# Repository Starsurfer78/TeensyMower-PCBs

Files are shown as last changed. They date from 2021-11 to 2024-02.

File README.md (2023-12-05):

DIY Robot Lawn Mower Community: https://www.diy-robot-lawn-mower.com/

# Teensymower PCB's - DIY Robot Lawn Mower (Teensy 4.1) 

The PCB's are designed to get you started on your own robotic lawnmower project. 
It doesn't matter if you want to convert a commercial mower or use a 3D printed housing.

The TeensyMainPCB is the brain of the mower to which all sensors and motors are connected.
The PowerPCB is responsible for the power supply and monitoring of the battery and the motors. 
The Wifi SenderPCB is responsible for the perimeter cable and goes into the charging station of the mower.

For your DIY project you need all 3 Boards.

RTK GPS is not yet possible at the moment

Only a few Electronic Parts are needed. 
- JST-XH Connectors
- Screw Terminal 5.04mm
- Resistors
- Pin Header Connector 2.54mm
- Active Buzzer
- LED
- Jumper
- Teensy 4.1
- ESP32 DEV Kit V1

Attention: 
The PCB's are still under development.
If you want to order your own PCBs, please check the forum first to see if there are any problems.
Use the PCBs at your own risk, no liability is assumed.

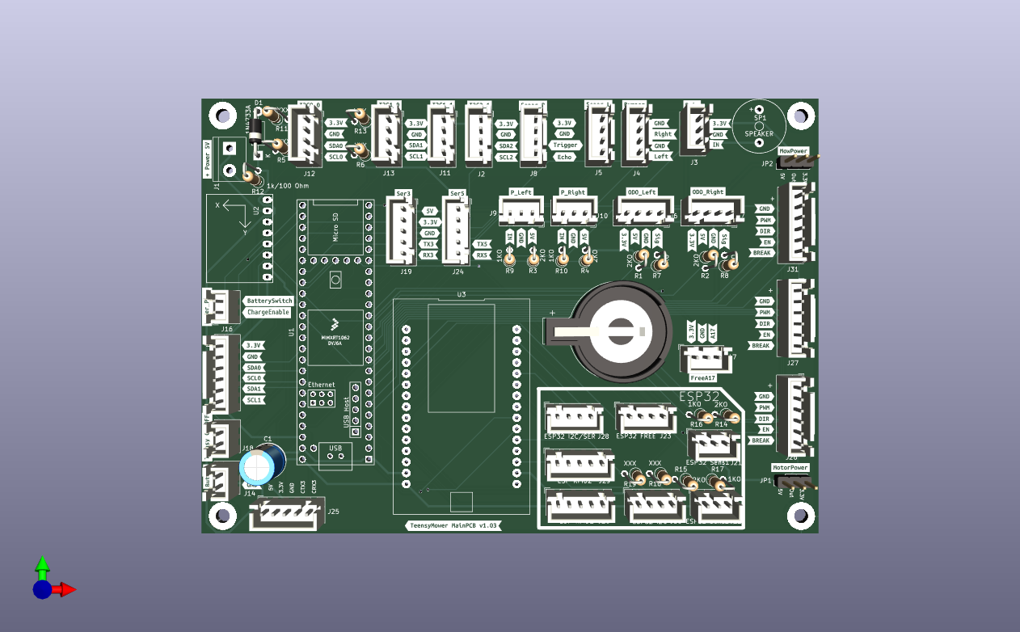
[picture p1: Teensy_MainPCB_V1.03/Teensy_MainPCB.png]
Vorschau Teensy PCB


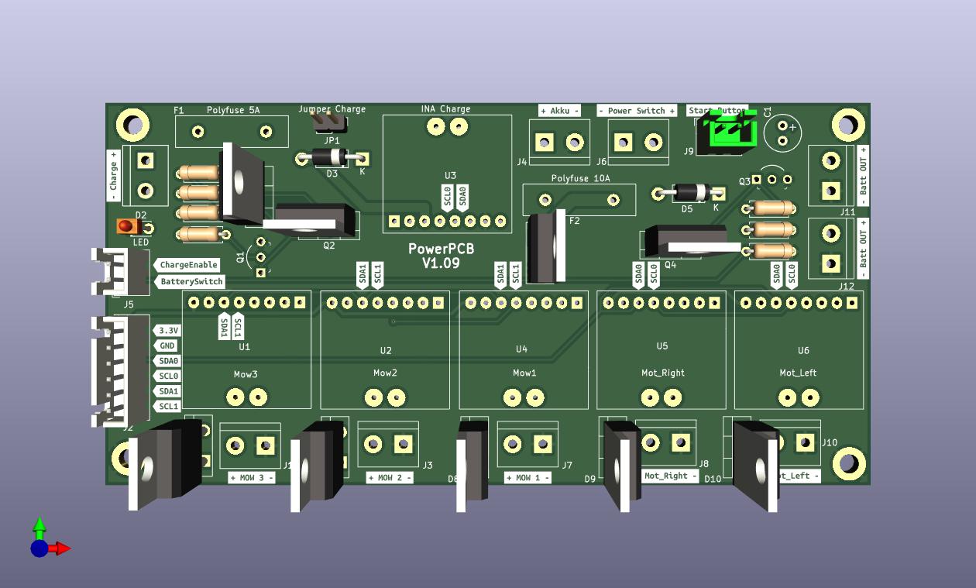
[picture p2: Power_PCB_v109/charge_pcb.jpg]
Vorschau Power PCB
)

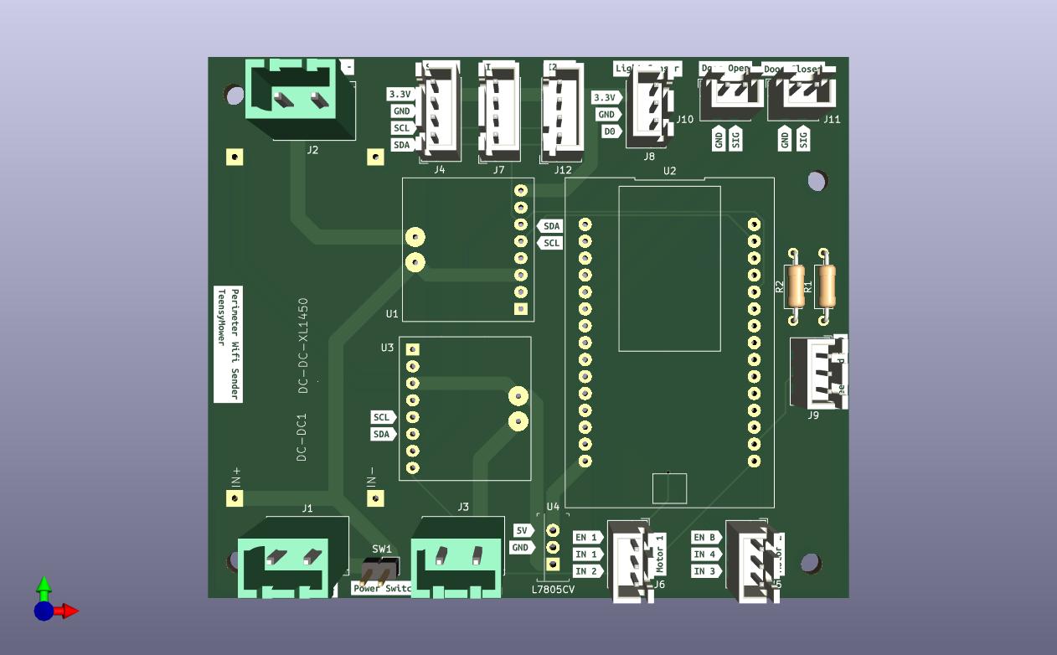
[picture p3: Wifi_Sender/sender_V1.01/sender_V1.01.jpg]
Vorschau WIFI Senderf PCB


Robomow RL2000:
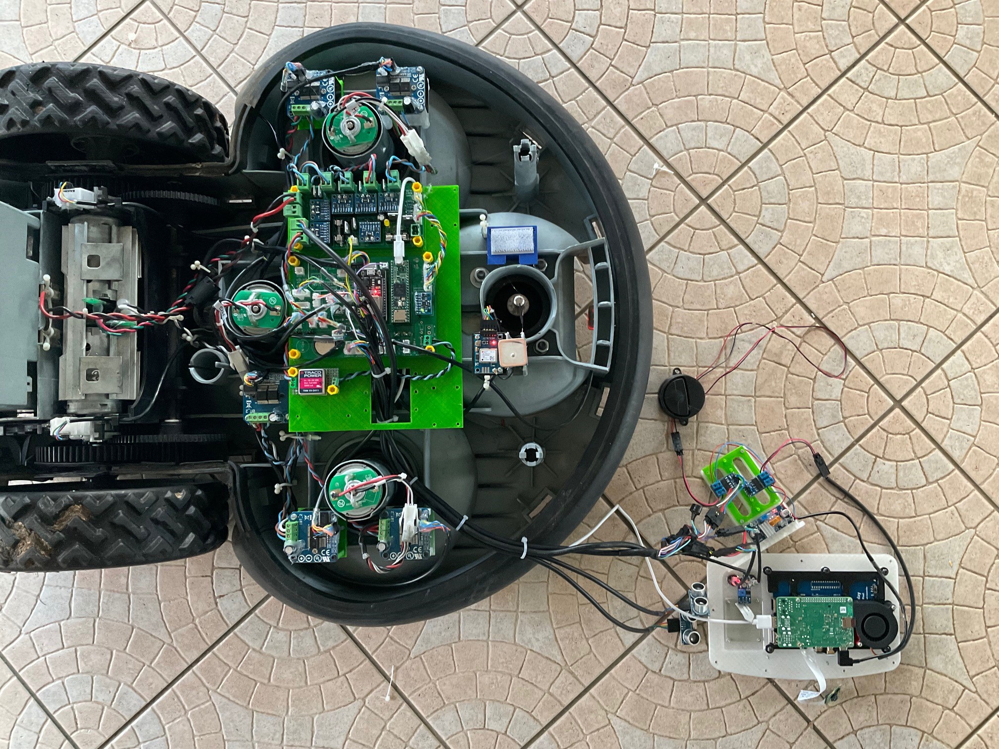
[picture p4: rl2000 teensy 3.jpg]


Tianchen TC-G158:
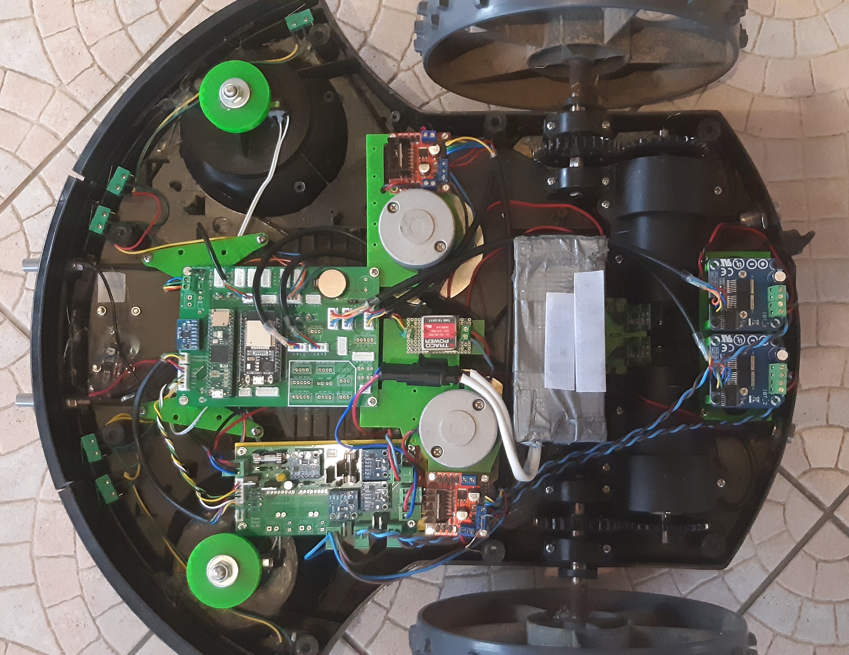
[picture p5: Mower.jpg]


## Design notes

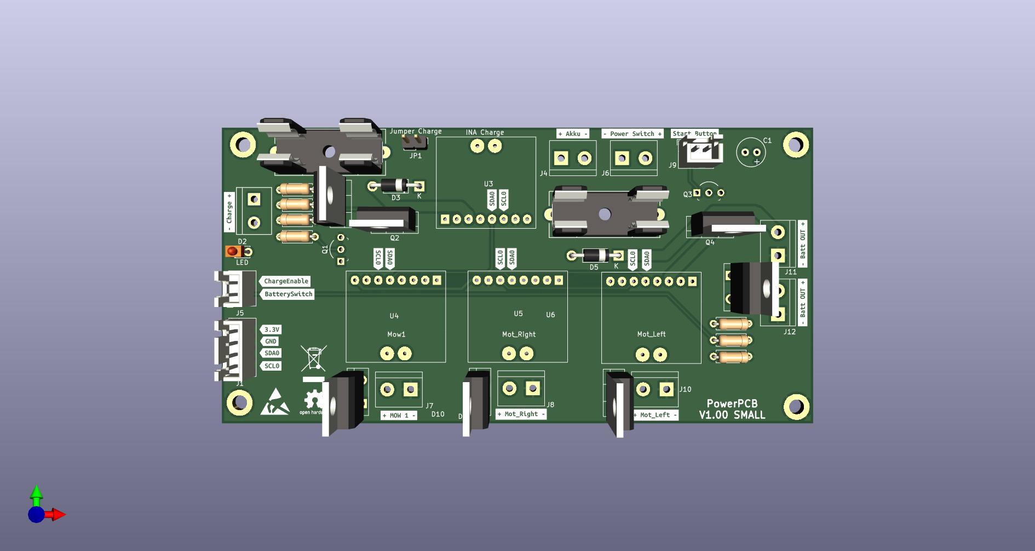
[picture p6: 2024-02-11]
Power_PCB_v100small/charge_pcb.jpg

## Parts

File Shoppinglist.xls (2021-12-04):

Quantidy | Name | Supplier
 | Präz.-Buchsenleisten 2,54 mm, 1X36, gerade | Reichelt (https://www.reichelt.de/praez-buchsenleisten-2-54-mm-1x36-gerade-mpe-115-1-036-p119957.html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)
 | 36pol. Stiftleiste, gerade, RM 2,54 | Reichelt (https://www.reichelt.de/36pol-stiftleiste-gerade-rm-2-54-sl-1x36g-2-54-p19504.html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)
 | Jumper 2,54 mm, geschlossen mit Griff | Reichelt (https://www.reichelt.de/jumper-2-54-mm-geschlossen-mit-griff-schwarz-mpe-149-4-002-f0-p119938.html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)
 | JST XH 2.54mm SET | Ebay (https://www.ebay.de/itm/203682351548?aid=1110006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)
 | JST XH 2.54mm 1x6 (PowerPCB) | Ebay (https://www.ebay.de/itm/194196796394?hash=item2d3707f3ea:g:1uUAAOSw9zZgwmGd)
 | Connection terminal system, 2-pin, spacing 5.08 | Reichelt (https://www.reichelt.de/de/en/connection-terminal-system-2-pin-spacing-5-08-akl-249-02-p36686.html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)
 | Box connector for AKL 249, 2-pin, spacing 5.08 | Reichelt (https://www.reichelt.de/de/en/box-connector-for-akl-249-2-pin-spacing-5-08-akl-220-02-p36693.html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)
 | LED Diode & Widerstände Sortiment Kit | Amazon (https://www.amazon.de/WayinTop-Widerstände-Sortiment-Arduino-Leuchtdiode/dp/B07YWX42RJ?pd)
 | Widerstand 1.5 Kohm | Amazon (https://www.amazon.de/gp/product/B07KX5B5DJ/ref=ppx_yo_dt_b_asin_title_o02_s00?ie=UTF8&psc=1)
 | Knopfzellenhalter Ø 20 mm | Reichelt (https://www.reichelt.de/knopfzellenhalter-fuer-20-mm-kzh-20-1-p44621.html?&trstct=pol_9&nbc=1)
 | INA226 | Amazon (https://www.amazon.de/gp/product/B07XM47JBW/ref=ppx_yo_dt_b_asin_title_o07_s01?ie=UTF8&psc=1)
 | INA3221 (Perimeter Sender) | Amazon (https://www.amazon.de/gp/product/B07XXFPNHC/ref=ppx_yo_dt_b_asin_title_o03_s01?ie=UTF8&psc=1)
 | 1N5819 Diode Schottky | Amazon (https://www.amazon.de/gp/product/B07KC2493L/ref=ppx_yo_dt_b_asin_title_o00_s00?ie=UTF8&psc=1)
 | IRF9540N 23 A 100 V | Amazon (https://www.amazon.de/gp/product/B086YW4TPD/ref=ppx_yo_dt_b_asin_title_o02_s00?ie=UTF8&psc=1)
 | MBR 1045 Schottkydiode, 45 V, 10 A | Reichelt (https://www.reichelt.de/schottkydiode-45-v-10-a-to-220ac-mbr-1045-p41944.html?search=MBR1045)
 | IRLB 8721 MOSFET, N-CH, TO-220, 30 V, 50 A, 65 W | Reichelt (https://www.reichelt.de/mosfet-n-ch-to-220-30-v-50-a-65-w-irlb-8721-p200919.html?search=IRLB+8721)
 | BC 547C Bipolartransistor, NPN, 45V, 0,1A, 0,5W | Reichelt (https://www.reichelt.de/bipolartransistor-npn-45v-0-1a-0-5w-to-92-bc-547c-p5007.html?search=BC547C)
 | Elko 100 uF, 100 V, 105°C | Reichelt (https://www.reichelt.de/de/en/e-cap-radial-100-uf-100-v-105-c-nhg-a-100u-100-p200367.html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)
 | Fuse holder, 5 x 20 mm, max. 6,3A/250V | Amazon (https://www.amazon.de/gp/product/B016UQPVLK/ref=ppx_yo_dt_b_asin_title_o01_s00?ie=UTF8&psc=1)
 | Glassicherung, 5 x 20 mm (10 A) | Amazon (https://www.amazon.de/SMIN-Stück-F10AL-Schnell-Blow-Sicherung/dp/B07Q98NDQQ?__mk_de_DE=ÅMÅŽÕÑ&s=diy)
 | Glassicherung, 5 x 20 mm (5 A) | Amazon (https://www.amazon.de/Stück-G-Sicherungseinsatz-Feinsicherung-5x20mm-522-524/dp/B01MV345Y5?__mk_de_DE=ÅMÅŽÕÑ&s=diy)
 | Buzzer 12mm 9,5mm RM 7,06 | Reichelt (https://www.reichelt.de/elektromagnetischer-summer-summer-tdb-05-p35918.html?&trstct=pol_0&nbc=1)
 | Push Button | Amazon (https://www.amazon.de/Larcele-Plastik-Momentary-Drücken-Druckknöpfe/dp/B077F7FT95)
 | Ein-Aus-Kippschalter | Amazon (https://www.amazon.de/Schalter-OFF-DPST-Terminals-wasserfester-Abdeckung/dp/B07438Q5ZZ?p)
 | Microswitch Bumper | Amazon (https://www.amazon.de/Hemobllo-Wasserdichter-Momentanschlag-Mikroschalter-Scharnierhebel/dp/B07LG18PN9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ÅMÅŽÕÑ)
 | Ultraschall JSN-SR04T (optional) | Amazon (https://www.amazon.de/gp/product/B08GLX5MHF/ref=ppx_yo_dt_b_asin_title_o08_s00?ie=UTF8&psc=1)
 | HC-SR04 Ultraschall (optional) | Amazon (https://www.amazon.de/AZDelivery-HC-SR04-Ultraschall-Entfernungsmesser-Raspberry/dp/B072N473HD)
 | Pn5180 NFC RFID (optional) | Amazon (https://www.amazon.de/gp/product/B07V1KZFNX/ref=ppx_yo_dt_b_asin_title_o09_s00?ie=UTF8&psc=1)
 | XL4015 5A DC-DC | Amazon (https://www.amazon.de/gp/product/B081JP5YZP/ref=ppx_yo_dt_b_asin_title_o08_s00?ie=UTF8&psc=1)
 | ESP32 DEV Kit v1 | Amazon (https://www.amazon.de/gp/product/B093GTDY9H/ref=ppx_yo_dt_b_asin_title_o01_s00?ie=UTF8&psc=1)
 | Teensy 4.1

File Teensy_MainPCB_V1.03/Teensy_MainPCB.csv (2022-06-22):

ID | Bezeichner | Gehäuse | Stückzahl | Bezeichnung | Anbieter und Referenz
1 | J2 | JST_XH_B4B-XH-A_1x04_P2.50mm_Vertical | 1 | I2C2_0
2 | J4 | JST_XH_B4B-XH-A_1x04_P2.50mm_Vertical | 1 | Bumper
3 | J5 | JST_XH_B4B-XH-A_1x04_P2.50mm_Vertical | 1 | Sonar_L
4 | J9 | JST_XH_B3B-XH-A_1x03_P2.50mm_Vertical | 1 | P_Left
5 | J10 | JST_XH_B3B-XH-A_1x03_P2.50mm_Vertical | 1 | P_Right
6 | J12 | JST_XH_B4B-XH-A_1x04_P2.50mm_Vertical | 1 | I2C0_0
7 | J13 | JST_XH_B4B-XH-A_1x04_P2.50mm_Vertical | 1 | I2C1_0
8 | J15 | JST_XH_B6B-XH-A_1x06_P2.50mm_Vertical | 1 | Power_PCB1
9 | R7,R8,R9,R10,R16,R17 | R_Axial_DIN0207_L6.3mm_D2.5mm_P2.54mm_Vertical | 6 | 1KO
10 | SP1 | Buzzer_12x9.5RM7.6 | 1 | SPEAKER
11 | J25 | JST_XH_B5B-XH-A_1x05_P2.50mm_Vertical | 1 | Can3
12 | J30 | JST_XH_B4B-XH-A_1x04_P2.50mm_Vertical | 1 | ESP32 I2C
13 | R2,R4,R1,R3,R14,R15 | R_Axial_DIN0207_L6.3mm_D2.5mm_P2.54mm_Vertical | 6 | 2KO
14 | H1,H2,H3,H4 | MountingHole_3.2mm_M3_Pad_TopBottom | 4 | MountingHole_Pad
15 | J31 | JST_XH_B6B-XH-A_1x06_P2.50mm_Vertical | 1 | Cutter
17 | J1 | TerminalBlock_bornier-2_P5.08mm | 1 | 5V IN
18 | J6 | JST_XH_B4B-XH-A_1x04_P2.50mm_Vertical | 1 | ODO_Left
19 | J7 | JST_XH_B4B-XH-A_1x04_P2.50mm_Vertical | 1 | ODO_Right
20 | J8 | JST_XH_B4B-XH-A_1x04_P2.50mm_Vertical | 1 | Sonar_R
21 | R5,R11 | R_Axial_DIN0207_L6.3mm_D2.5mm_P2.54mm_Vertical | 2 | XXXX
22 | R6,R13,R18,R19 | R_Axial_DIN0207_L6.3mm_D2.5mm_P2.54mm_Vertical | 4 | XXX
23 | R12 | R_Axial_DIN0207_L6.3mm_D2.5mm_P2.54mm_Vertical | 1 | 1k/100 Ohm
25 | J3 | JST_XH_B3B-XH-A_1x03_P2.50mm_Vertical | 1 | Rain
26 | J16 | JST_XH_B2B-XH-A_1x02_P2.50mm_Vertical | 1 | Power_PCB2
27 | BT1 | BatteryHolder_Keystone_103_1x20mm | 1 | Battery_Cell
28 | J17 | JST_XH_B3B-XH-A_1x03_P2.50mm_Vertical | 1 | FreeA17
29 | J20 | JST_XH_B5B-XH-A_1x05_P2.50mm_Vertical | 1 | ESP RFID1
30 | J21 | JST_XH_B3B-XH-A_1x03_P2.50mm_Vertical | 1 | ESP32 Sens1
31 | J18 | JST_XH_B2B-XH-A_1x02_P2.50mm_Vertical | 1 | Teensy On/Off
32 | J22 | JST_XH_B3B-XH-A_1x03_P2.50mm_Vertical | 1 | ESP32 Sens2
33 | J23 | JST_XH_B4B-XH-A_1x04_P2.50mm_Vertical | 1 | ESP32 FREE
34 | J24 | JST_XH_B5B-XH-A_1x05_P2.50mm_Vertical | 1 | Ser5
35 | J26 | JST_XH_B6B-XH-A_1x06_P2.50mm_Vertical | 1 | Motor_Right
36 | J27 | JST_XH_B6B-XH-A_1x06_P2.50mm_Vertical | 1 | Motor_Left
37 | J28 | JST_XH_B4B-XH-A_1x04_P2.50mm_Vertical | 1 | ESP32 I2C/SER
39 | D1 | D_DO-41_SOD81_P10.16mm_Horizontal | 1 | 1N4733A
40 | J11 | JST_XH_B4B-XH-A_1x04_P2.50mm_Vertical | 1 | I2C1_1
41 | JP1 | PinHeader_1x03_P2.54mm_Vertical | 1 | MotorPower
42 | JP2 | PinHeader_1x03_P2.54mm_Vertical | 1 | CutterPower
43 | J19 | JST_XH_B5B-XH-A_1x05_P2.50mm_Vertical | 1 | Ser3
44 | J29 | JST_XH_B5B-XH-A_1x05_P2.50mm_Vertical | 1 | ESP RFID2
45 | J14 | JST_XH_B2B-XH-A_1x02_P2.50mm_Vertical | 1 | Button
46 | C1 | CP_Radial_D8.0mm_P3.80mm | 1 | CP1

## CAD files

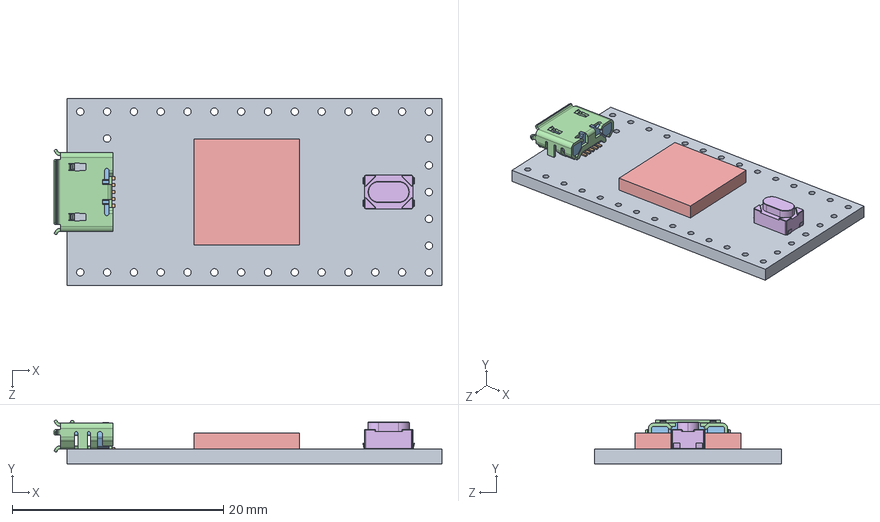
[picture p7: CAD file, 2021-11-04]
Wifi_Sender/sender_V1.01/teensy.pretty-master/Teensy_4.0_Assembly.STEP
36.8 x 4.12 x 17.7 mm
Teensy_4.0_PCB
Micro USB-B Female 5Pin SMD
NXP iMXRT1062
SKRPACE010 v4

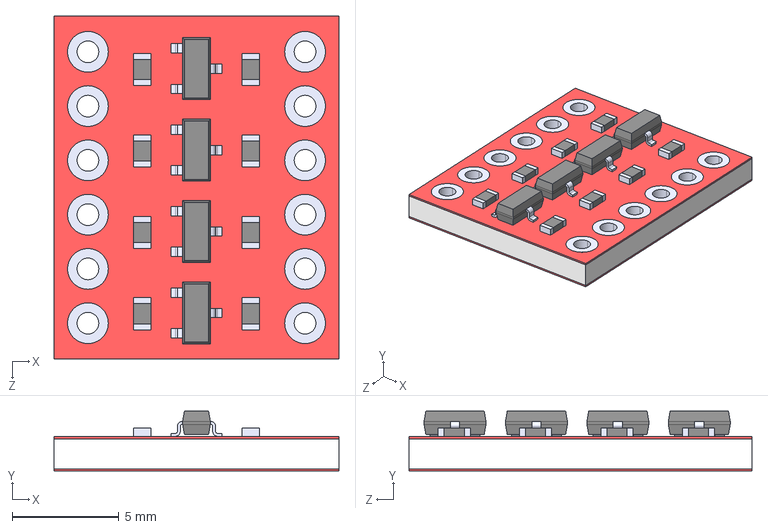
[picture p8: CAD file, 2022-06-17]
Teensy_MainPCB_V1.03/BOB-12009.step
13.3 x 2.80 x 16.1 mm

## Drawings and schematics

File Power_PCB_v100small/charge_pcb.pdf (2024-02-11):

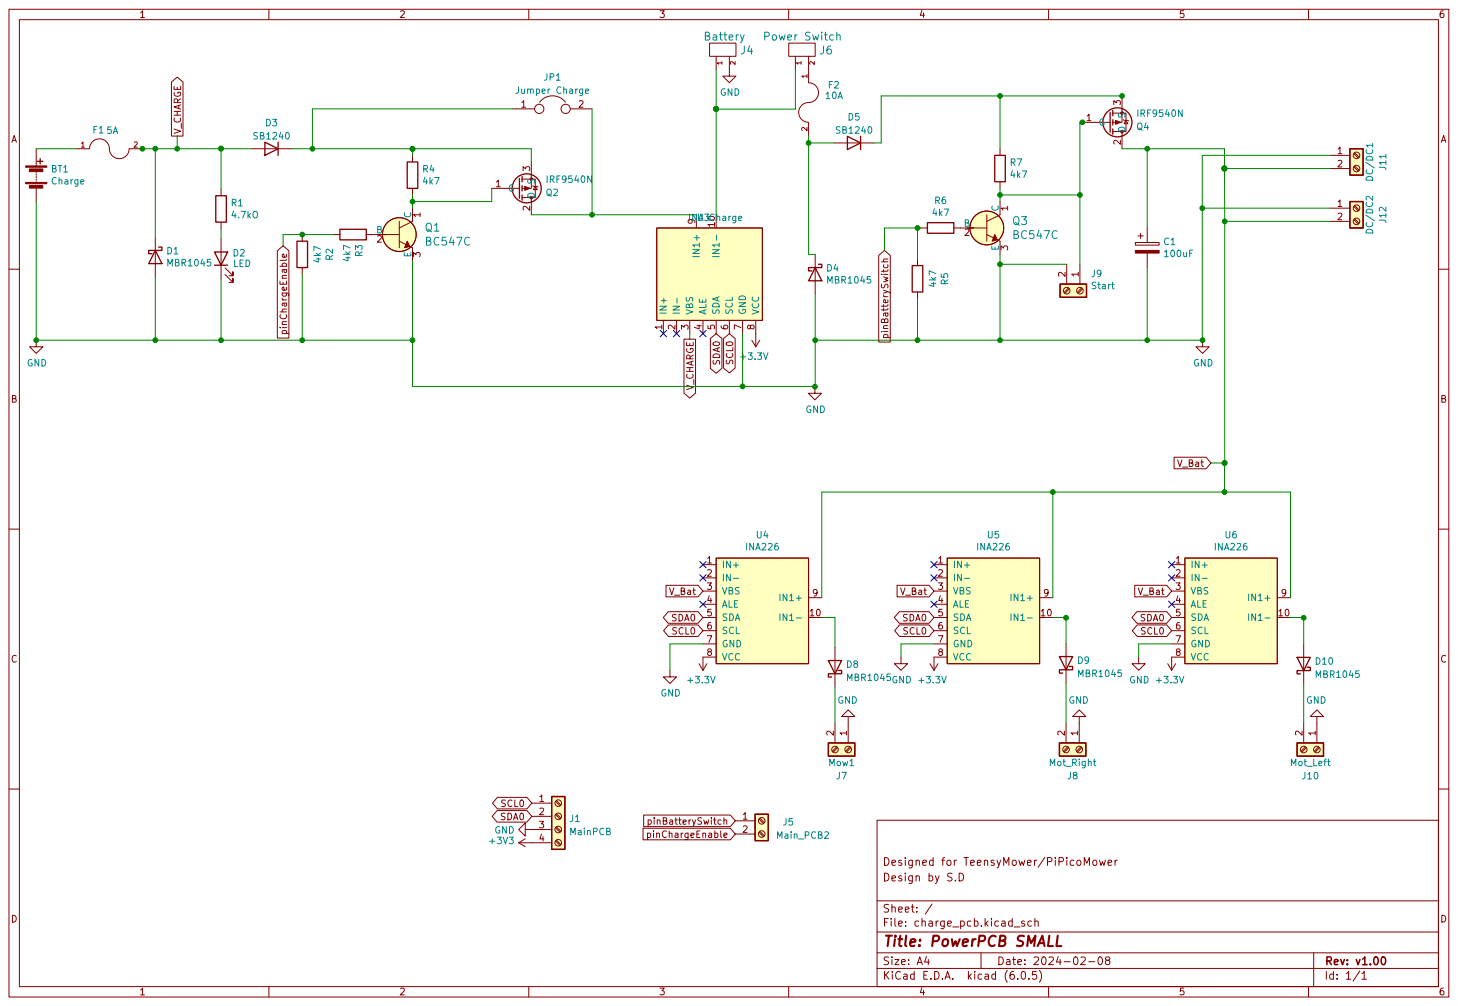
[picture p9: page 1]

File: charge_pcb.kicad_sch Sheet: / Design by S.D

Id: 1/1 Title: PowerPCB SMALL

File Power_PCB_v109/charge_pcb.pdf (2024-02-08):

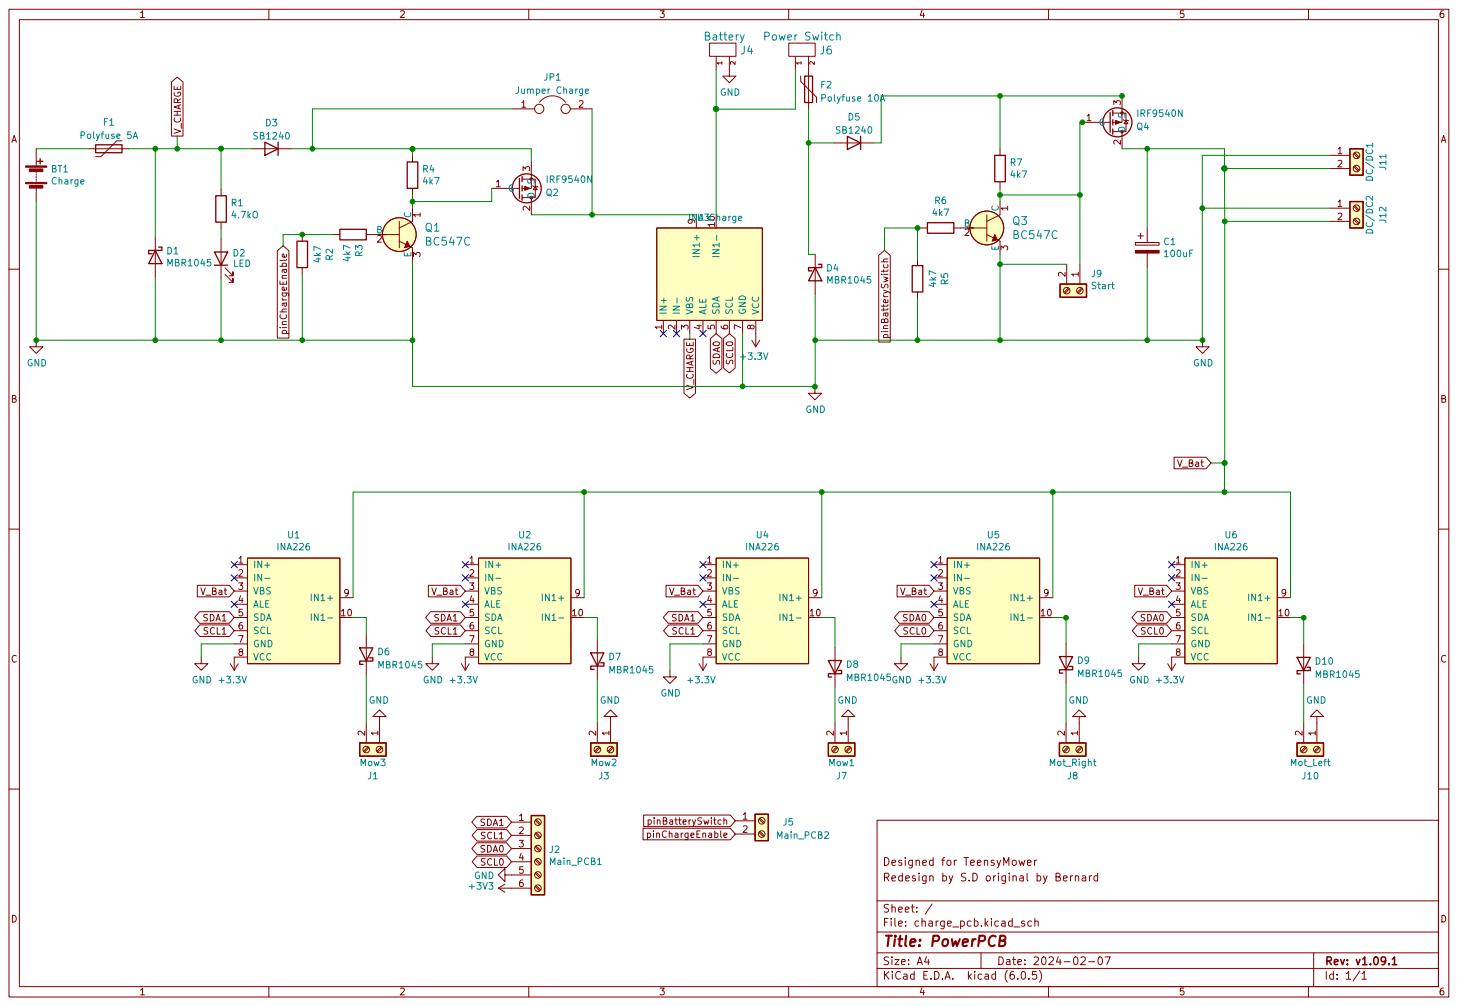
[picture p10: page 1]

Designed for TeensyMower
File: charge_pcb.kicad_sch Sheet: / Redesign by S.D original by Bernard

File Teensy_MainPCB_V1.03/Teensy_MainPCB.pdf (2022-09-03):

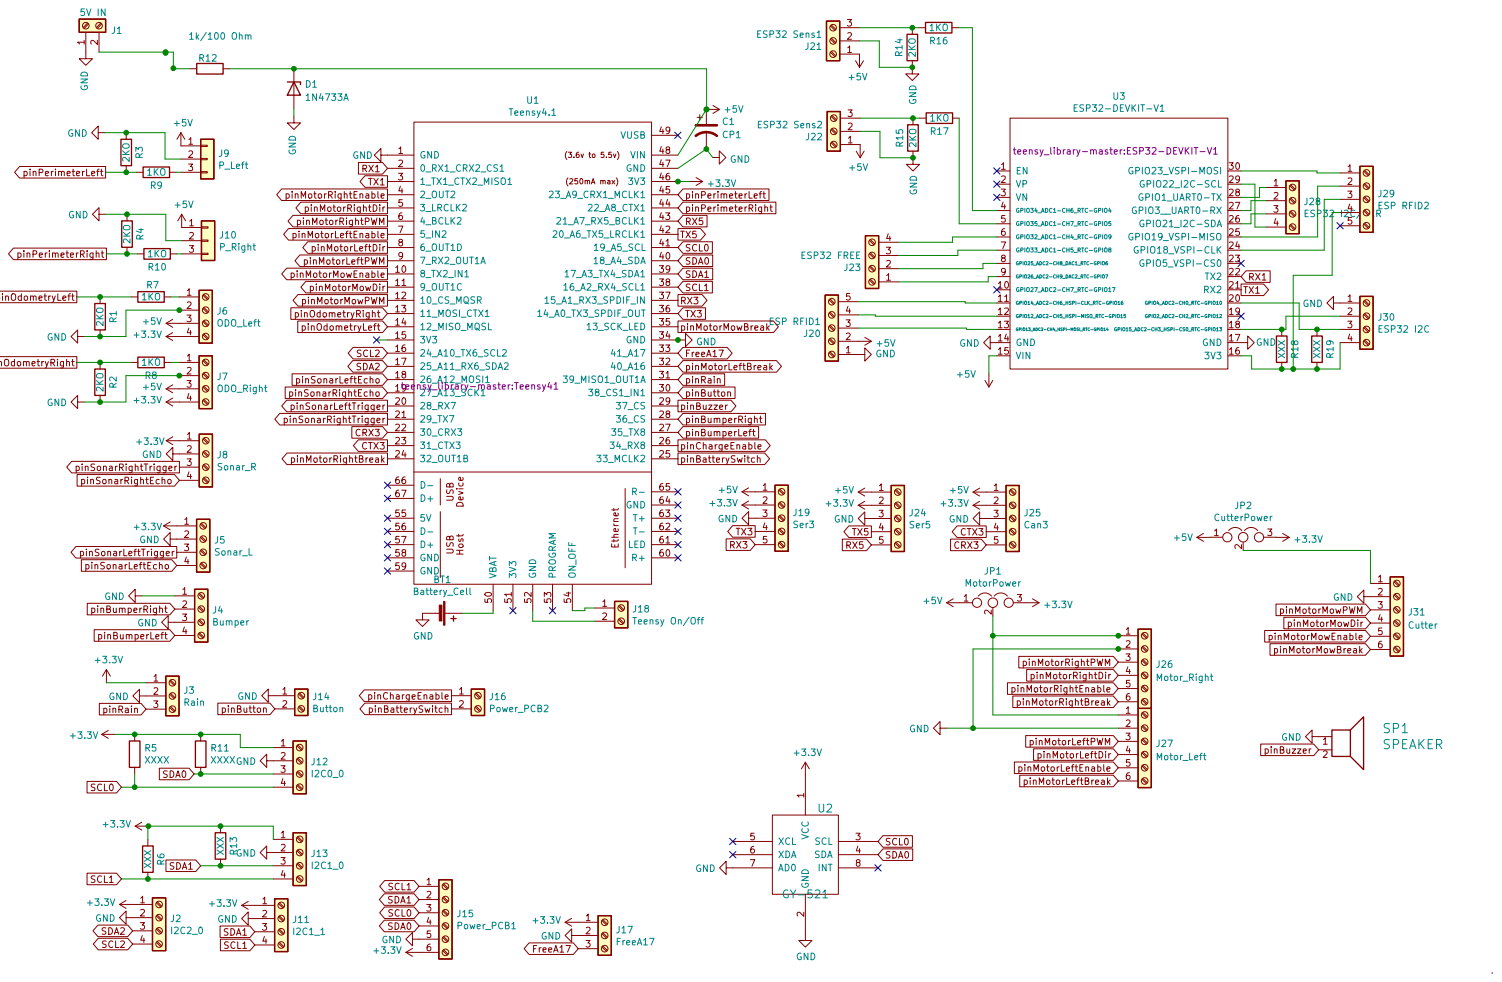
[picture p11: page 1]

5V IN GND GND
teensy_library-master:ESP32-DEVKIT-V1 GND GND

2 SCL 3 SDA 4 XCL 5 XDA 6 AD0 7

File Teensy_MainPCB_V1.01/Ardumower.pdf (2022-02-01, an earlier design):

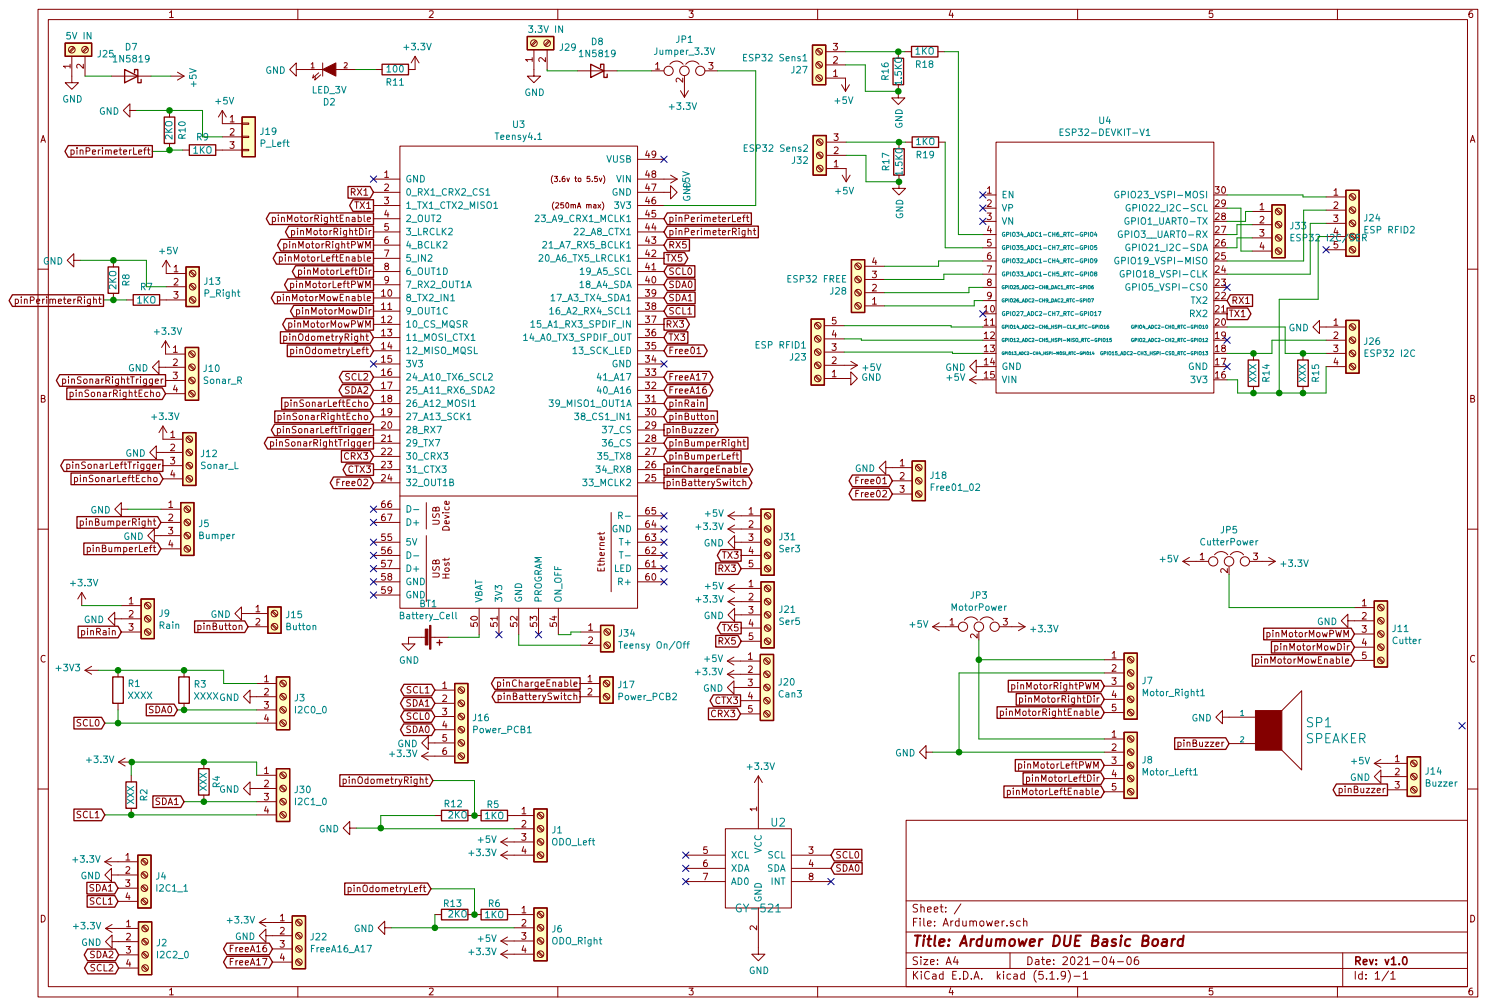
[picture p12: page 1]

J15 Button GND GNDGND GND
pinBumperRight

2 SCL 3 SDA 4 XCL 5 XDA 6 AD0 7

Id: 1/1 Title: Ardumower DUE Basic Board

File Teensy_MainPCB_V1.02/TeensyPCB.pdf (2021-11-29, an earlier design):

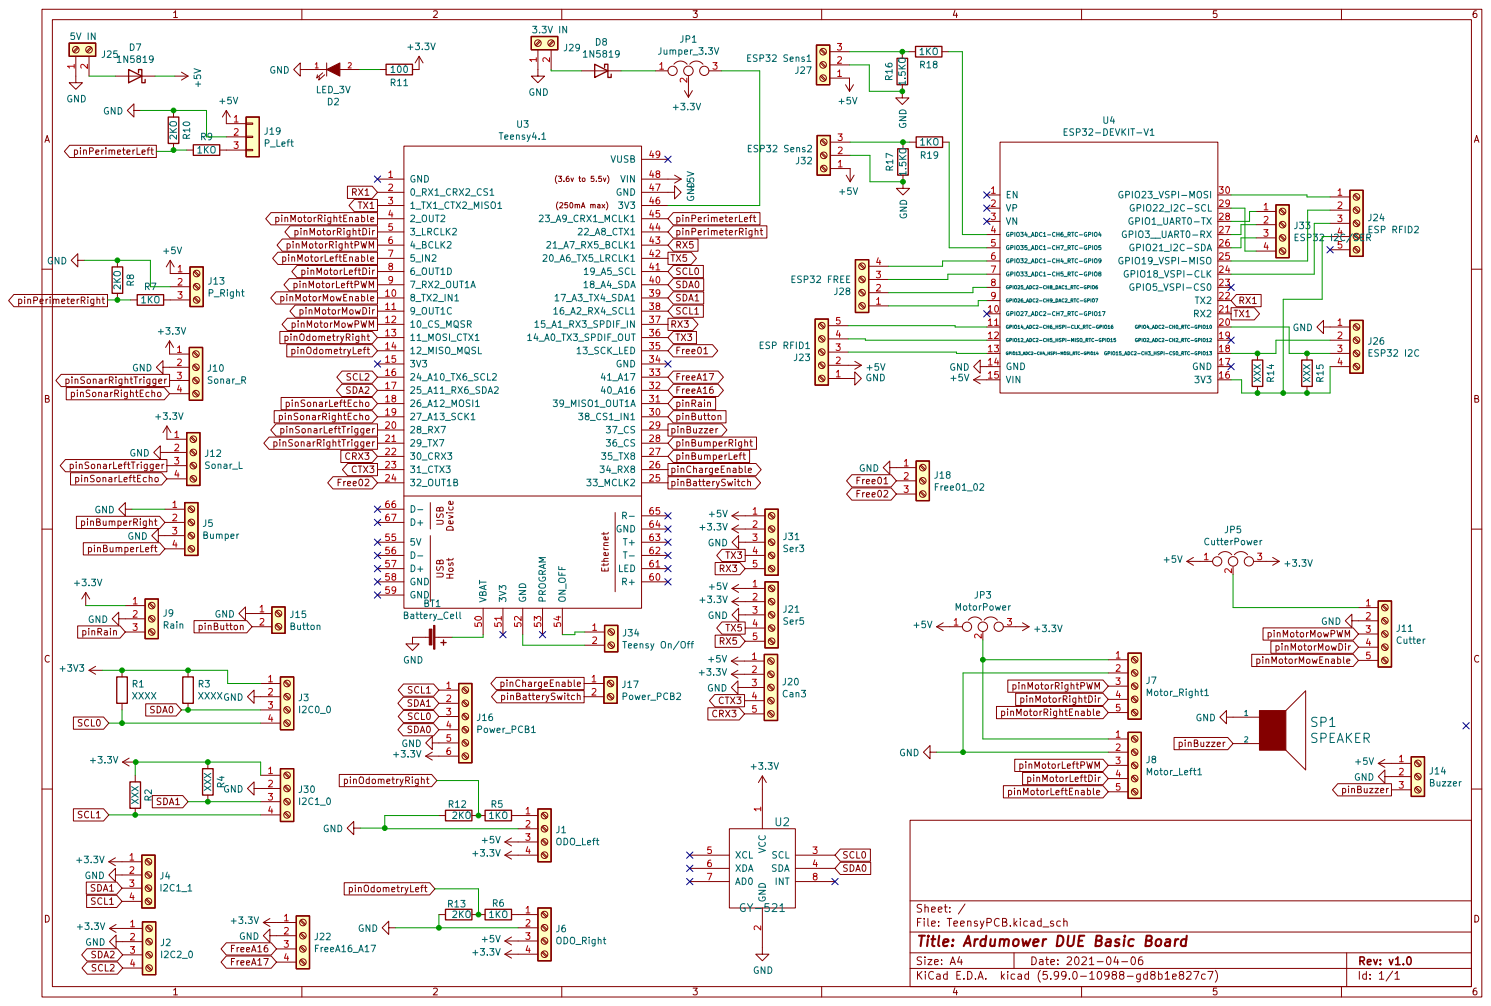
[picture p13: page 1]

2 SCL 3 SDA 4 XCL 5 XDA 6 AD0 7

File: TeensyPCB.kicad_sch Sheet: /
Id: 1/1 Title: Ardumower DUE Basic Board

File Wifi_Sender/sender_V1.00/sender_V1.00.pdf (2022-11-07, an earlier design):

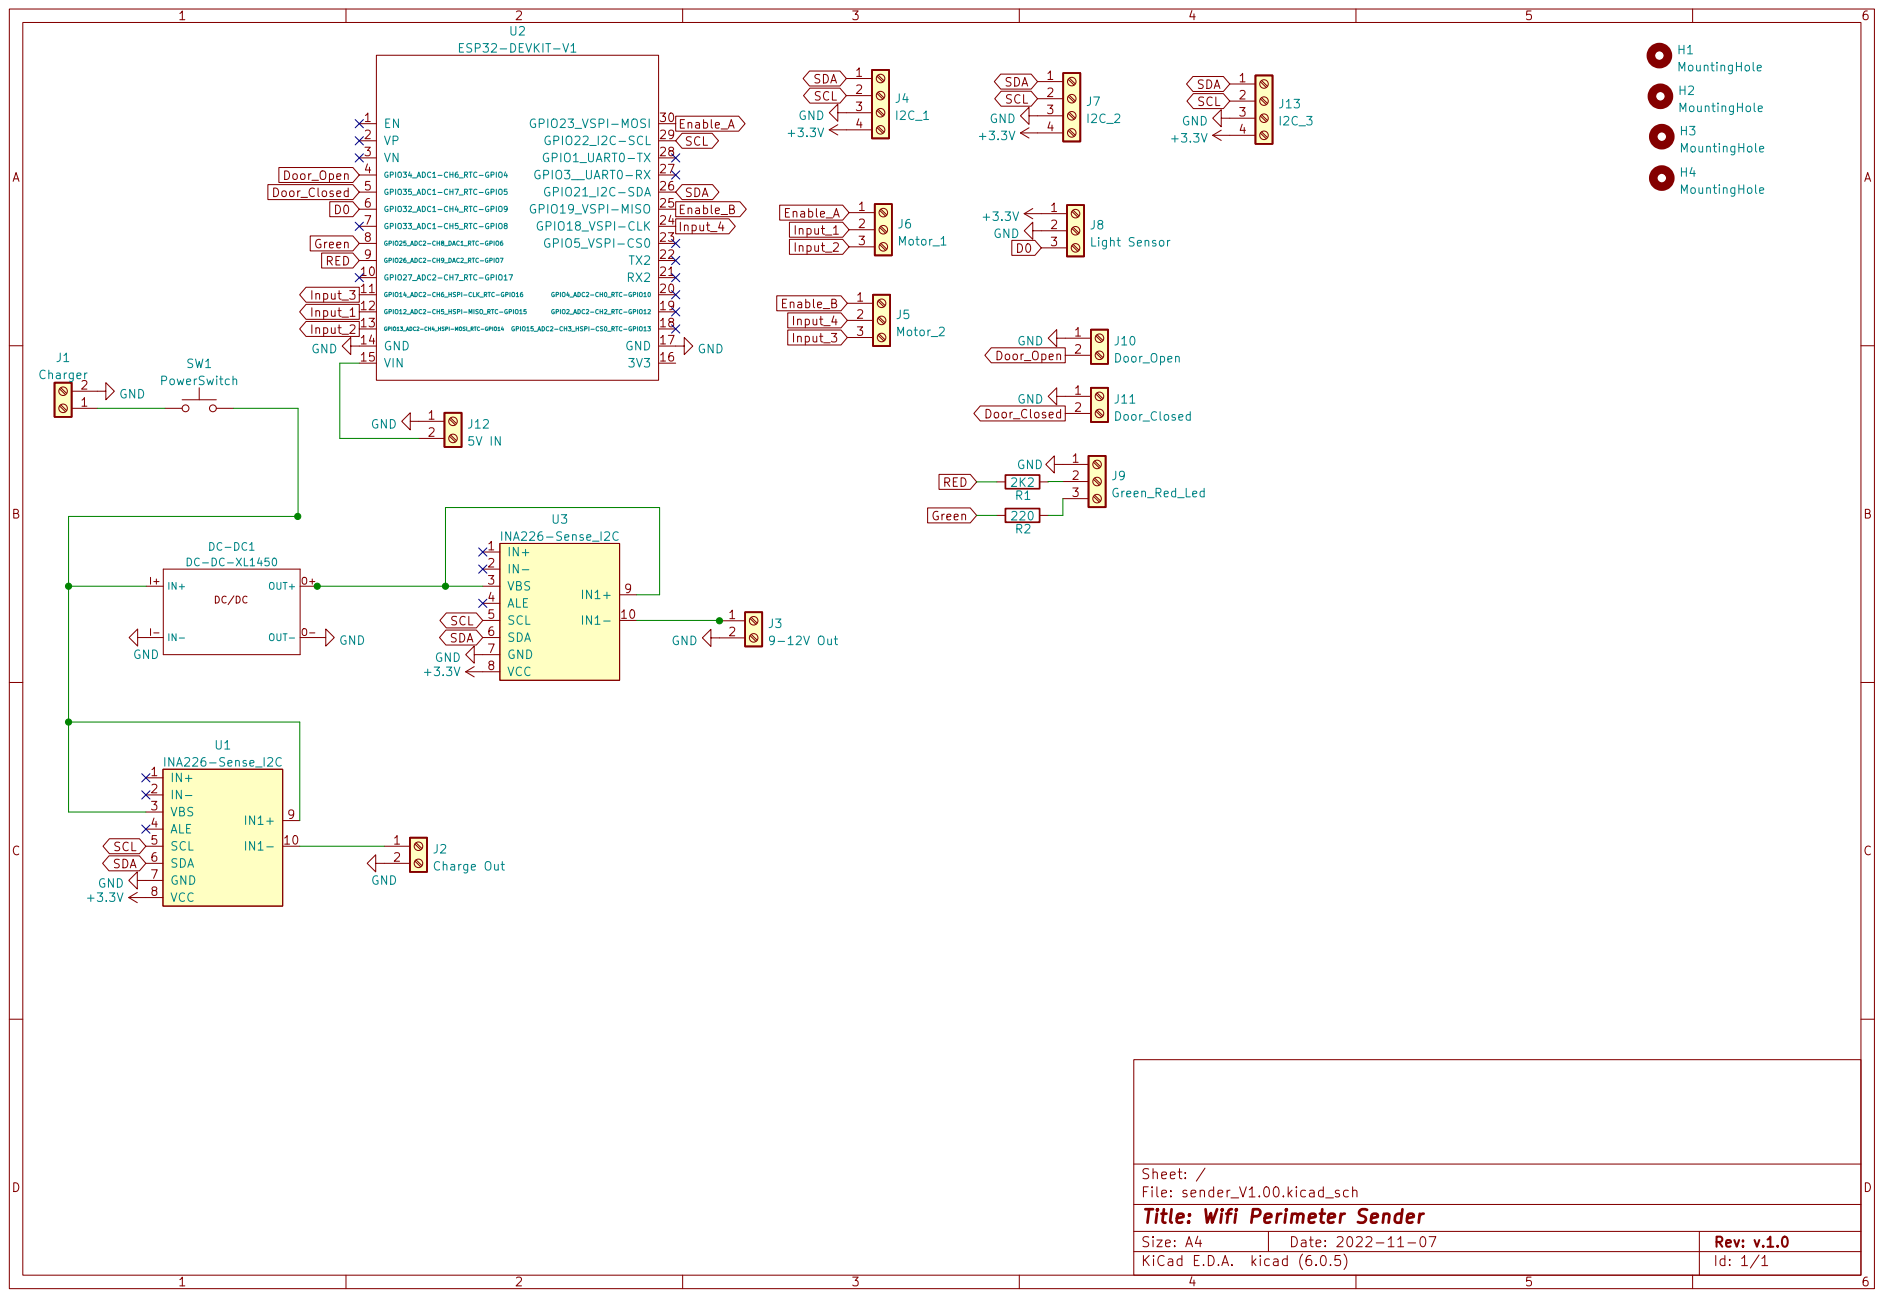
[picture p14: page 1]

File: sender_V1.00.kicad_sch Sheet: /
Id: 1/1 Title: Wifi Perimeter Sender

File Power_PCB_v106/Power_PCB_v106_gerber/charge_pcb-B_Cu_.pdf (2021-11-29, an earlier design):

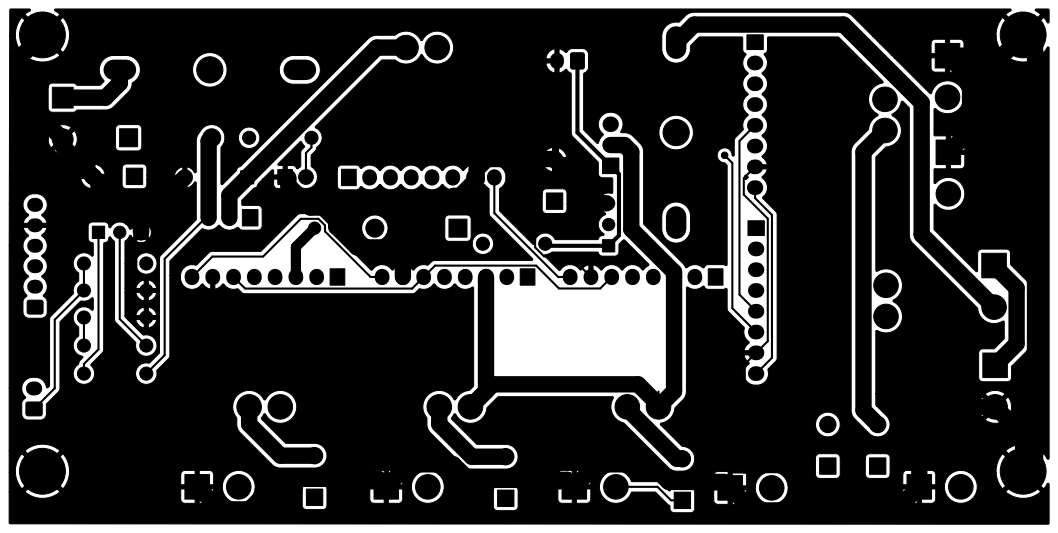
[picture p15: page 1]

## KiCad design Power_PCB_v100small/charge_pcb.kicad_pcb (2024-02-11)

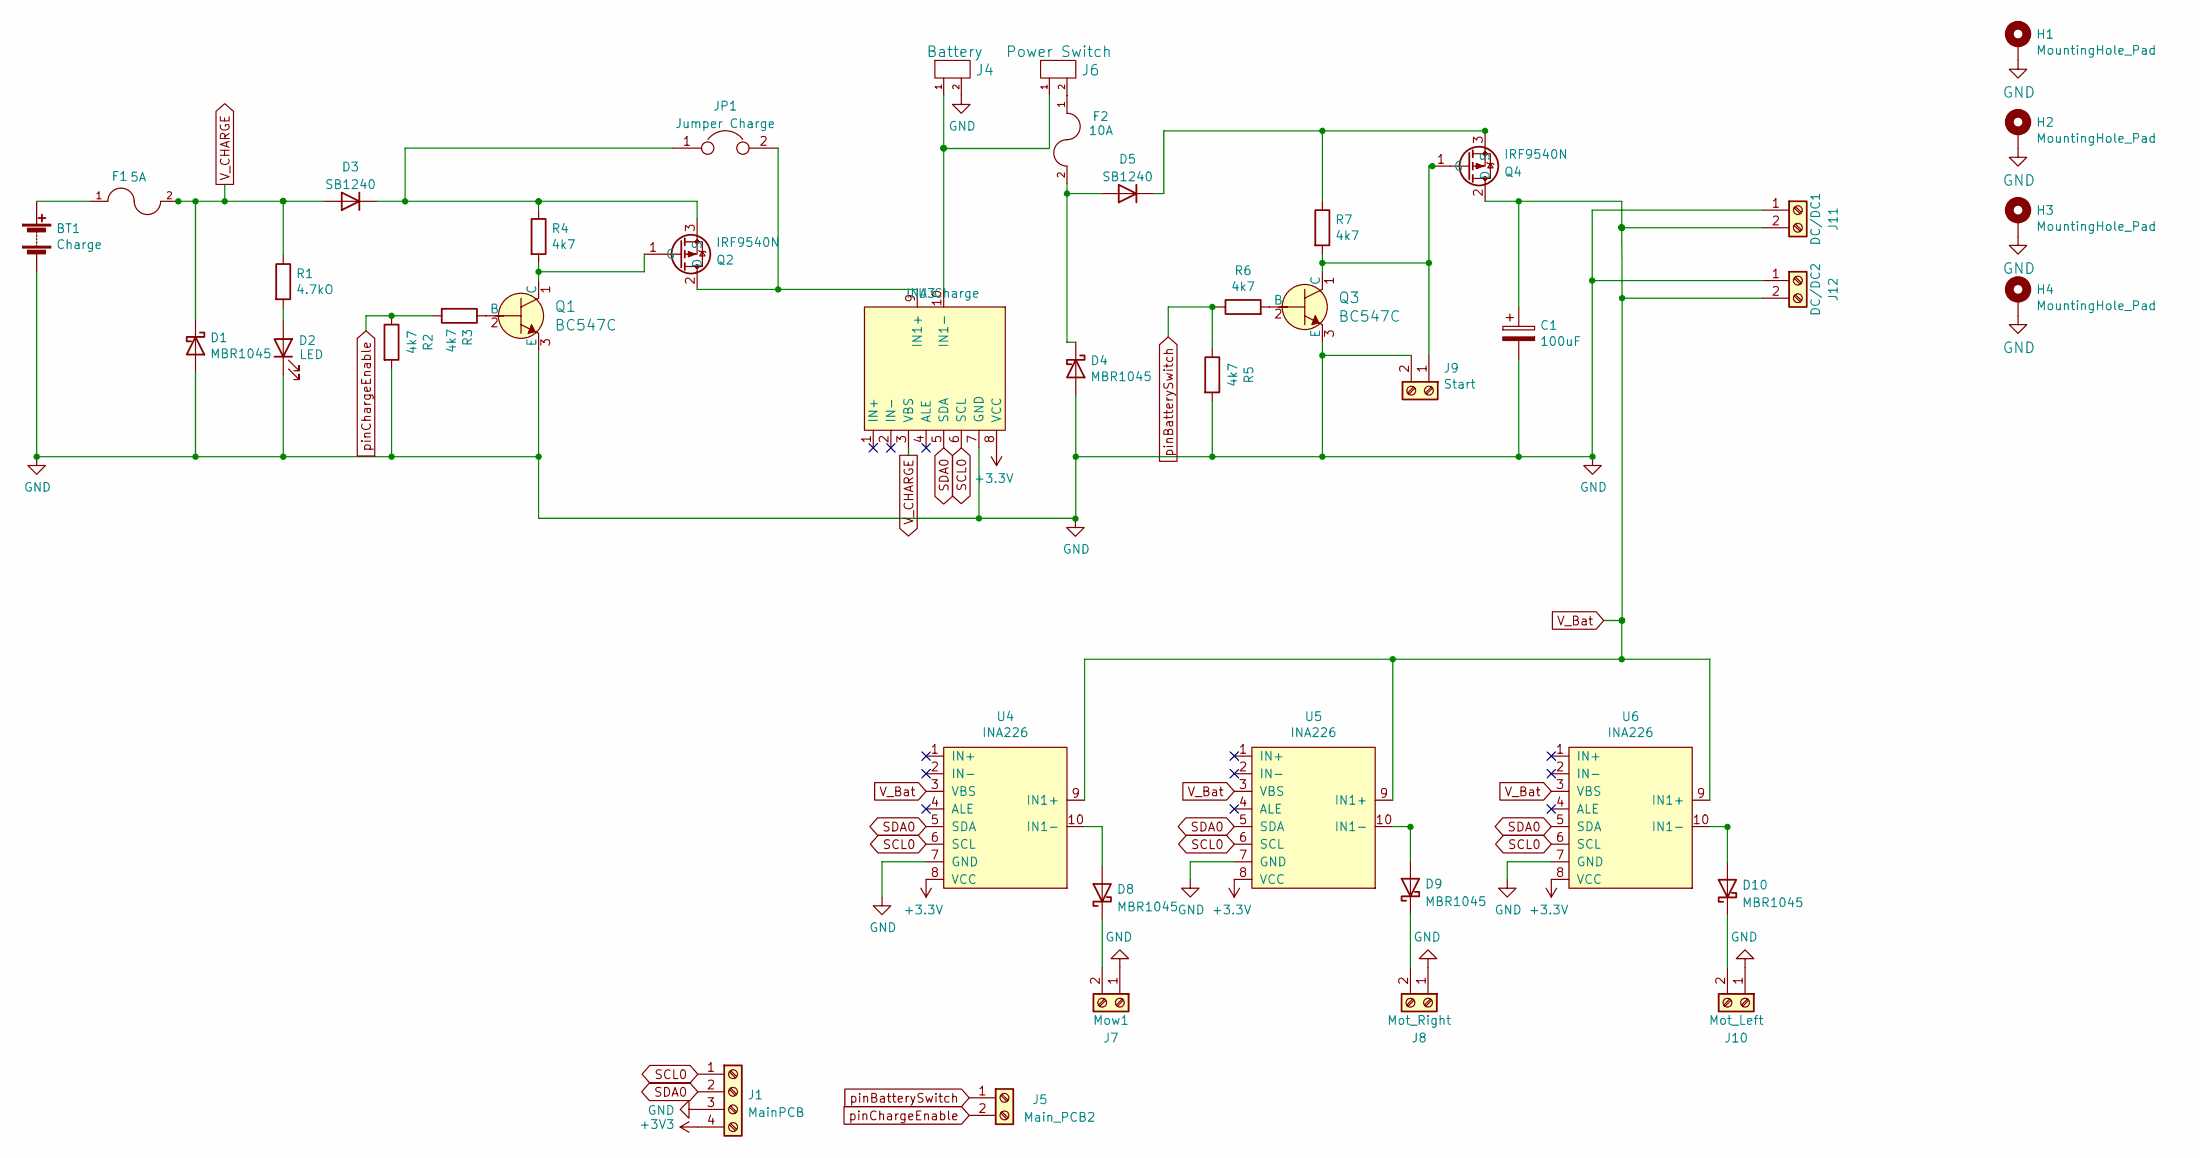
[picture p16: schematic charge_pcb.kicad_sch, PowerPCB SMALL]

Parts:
BT1: Charge; Anschlussklemme_2P_RM5,08
C1: 100uF; Elko_vert_11.2x6.3mm_RM2.5
D1, D4, D8, D9, D10: MBR1045; TO-220-2_Vertical
D2: LED; LED_D1.8mm_W3.3mm_H2.4mm
D3, D5: SB1240; D_DO-41_SOD81_P10.16mm_Horizontal
F1: 5A; Fuseholder_Reichelt_PL112000
F2: 10A; Fuseholder_Reichelt_PL112000
H1, H2, H3, H4: MountingHole_Pad; MountingHole_3.2mm_M3_DIN965_Pad_TopBottom
J1: MainPCB; JST_XH_B4B-XH-A_1x04_P2.50mm_Vertical
J4: Battery; TerminalBlock_bornier-2_P5.08mm
J5: Main_PCB2; JST_XH_B2B-XH-A_1x02_P2.50mm_Vertical
J6: Power Switch; TerminalBlock_bornier-2_P5.08mm
J7: Mow1; TerminalBlock_bornier-2_P5.08mm
J8: Mot_Right; TerminalBlock_bornier-2_P5.08mm
J9: Start; JST_XH_B2B-XH-A_1x02_P2.50mm_Vertical
J10: Mot_Left; TerminalBlock_bornier-2_P5.08mm
J11: DC/DC1; TerminalBlock_bornier-2_P5.08mm
J12: DC/DC2; TerminalBlock_bornier-2_P5.08mm
JP1: Jumper Charge; PinHeader_1x02_P2.54mm_Vertical
Q1, Q3: BC547C; TO-92-3_Formed_Leads; MPN BC548BTA; Digi-Key_PN BC548BTACT-ND
Q2, Q4: IRF9540N; TO-220-3_Vertical
R1: 4.7kO; R_Axial_DIN0207_L6.3mm_D2.5mm_P7.62mm_Horizontal
R2, R3, R4, R5, R6, R7: 4k7; R_Axial_DIN0207_L6.3mm_D2.5mm_P7.62mm_Horizontal
U3: INA Charge; INA226
U4, U5, U6: INA226

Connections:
GND: BT1.2 (-), C1.2, D1.2 (A), D2.1 (K), D4.2 (A), H1.1, H2.1, H3.1, H4.1, J1.3, J4.2, J7.1, J8.1, J9.2, J10.1, J11.1, J12.1, Q1.3 (E), Q3.3 (E), R2.2, R5.2, U3.7 (GND), U4.7 (GND), U5.7 (GND), U6.7 (GND)
unnamed: BT1.1 (+), F1.1
unnamed: D2.2 (A), R1.2
unnamed: D3.1 (K), JP1.1, Q2.3 (S), R4.1
unnamed: D4.1 (K), D5.2 (A), F2.2
unnamed: D5.1 (K), Q4.3 (S), R7.1
unnamed: D8.1 (K), J7.2
unnamed: D8.2 (A), U4.10 (IN1-)
unnamed: D9.1 (K), J8.2
unnamed: D9.2 (A), U5.10 (IN1-)
unnamed: D10.1 (K), J10.2
unnamed: D10.2 (A), U6.10 (IN1-)
unnamed: J4.1, J6.1, U3.10 (IN1-)
unnamed: F2.1, J6.2
unnamed: J9.1, Q3.1 (C), Q4.1 (G), R7.2
unnamed: JP1.2, Q2.2 (D), U3.9 (IN1+)
unnamed: Q1.1 (C), Q2.1 (G), R4.2
unnamed: Q1.2 (B), R3.1
unnamed: Q3.2 (B), R6.2
SCL0: J1.1, U3.6 (SCL), U4.6 (SCL), U5.6 (SCL), U6.6 (SCL)
SDA0: J1.2, U3.5 (SDA), U4.5 (SDA), U5.5 (SDA), U6.5 (SDA)
V_Bat: C1.1, J11.2, J12.2, Q4.2 (D), U4.3 (VBS), U4.9 (IN1+), U5.3 (VBS), U5.9 (IN1+), U6.3 (VBS), U6.9 (IN1+)
V_CHARGE: D1.1 (K), D3.2 (A), F1.2, R1.1, U3.3 (VBS)
pinBatterySwitch: J5.1, R5.1, R6.1
pinChargeEnable: J5.2, R2.1, R3.2

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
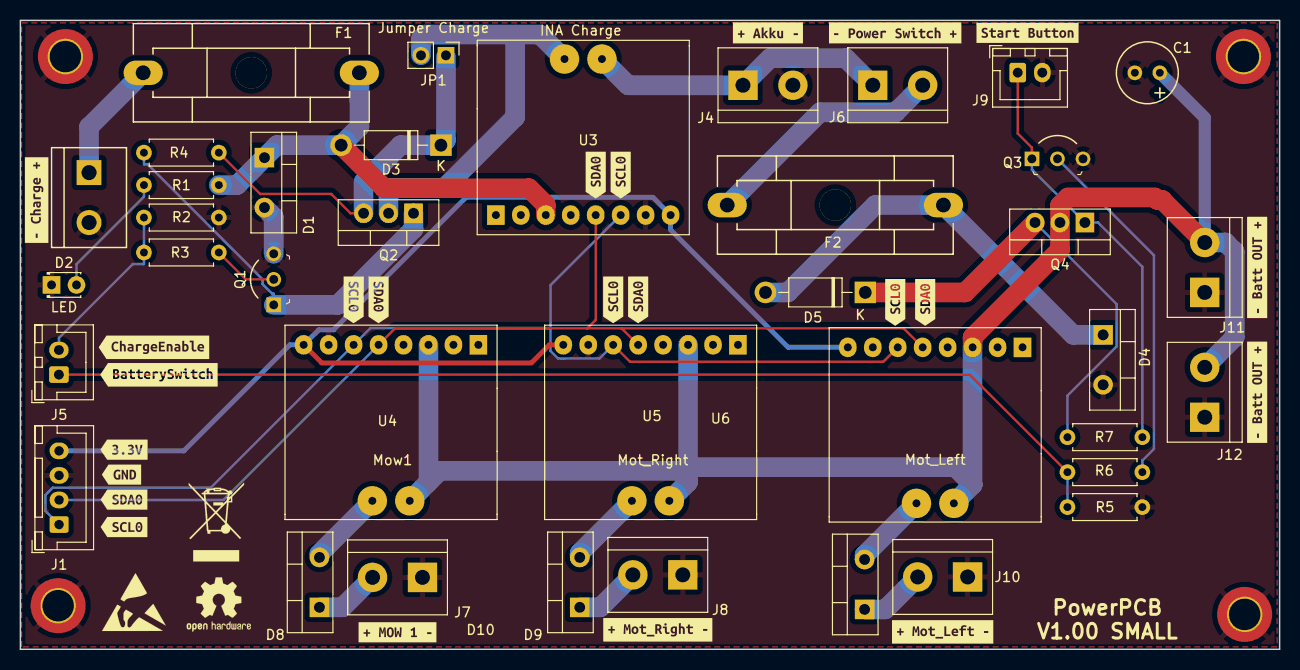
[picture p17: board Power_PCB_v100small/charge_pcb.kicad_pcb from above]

Board: 2 copper layers, 128.1 x 64.0 mm, 65 parts (0 on the bottom side), 26 nets.

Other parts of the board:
kibuzzard-62B75E62: G***; kibuzzard-62B75E62
kibuzzard-62B75EB1: G***; kibuzzard-62B75EB1
kibuzzard-65C504B9: G***; kibuzzard-65C504B9
kibuzzard-65C5049A: G***; kibuzzard-65C5049A
kibuzzard-630F6B1E: G***; kibuzzard-630F6B1E
kibuzzard-630F6B3C: G***; kibuzzard-630F6B3C
kibuzzard-630F6FC9: G***; kibuzzard-630F6FC9
kibuzzard-630F68E0: G***; kibuzzard-630F68E0
kibuzzard-630F70A7: G***; kibuzzard-630F70A7
kibuzzard-630F714A: G***; kibuzzard-630F714A
kibuzzard-630F6257: G***; kibuzzard-630F6257
kibuzzard-630F6901: G***; kibuzzard-630F6901
kibuzzard-630F6915: G***; kibuzzard-630F6915
kibuzzard-630F6938: G***; kibuzzard-630F6938
kibuzzard-630F7110: G***; kibuzzard-630F7110
kibuzzard-630FA3ED: G***; kibuzzard-630FA3ED
kibuzzard-630FA50E: G***; kibuzzard-630FA50E
kibuzzard-630FA52F: G***; kibuzzard-630FA52F
kibuzzard-630FA55C: G***; kibuzzard-630FA55C
kibuzzard-630FA420: G***; kibuzzard-630FA420
kibuzzard-630FA573: G***; kibuzzard-630FA573
kibuzzard-6311B784: G***; kibuzzard-6311B784
kibuzzard-6311B799: G***; kibuzzard-6311B799

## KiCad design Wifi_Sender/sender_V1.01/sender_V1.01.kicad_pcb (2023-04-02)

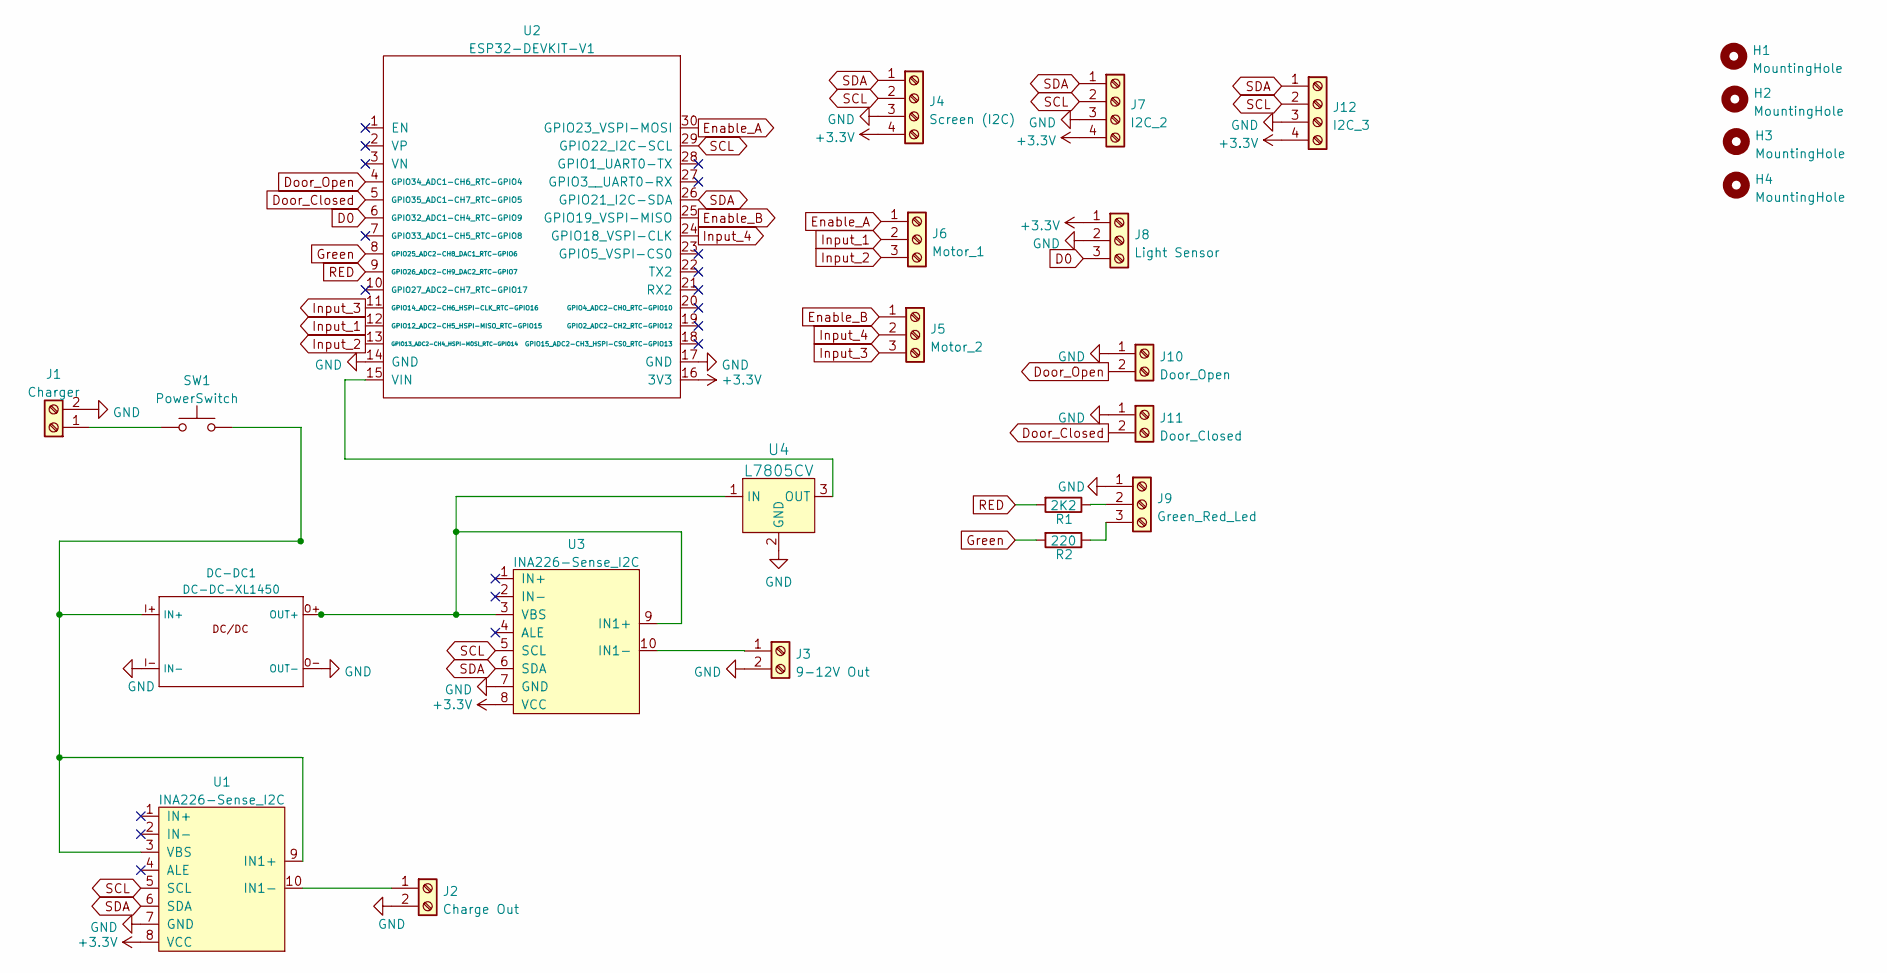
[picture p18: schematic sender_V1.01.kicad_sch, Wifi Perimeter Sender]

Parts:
DC-DC1: DC-DC-XL1450; DCDC-XL1450
H1, H2, H3, H4: MountingHole; MountingHole_3.2mm_M3
J1: Charger; PhoenixContact_MSTBVA_2,5_2-G-5,08_1x02_P5.08mm_Vertical
J2: Charge Out; PhoenixContact_MSTBVA_2,5_2-G-5,08_1x02_P5.08mm_Vertical
J3: 9-12V Out; PhoenixContact_MSTBVA_2,5_2-G-5,08_1x02_P5.08mm_Vertical
J4: Screen (I2C); JST_XH_B4B-XH-A_1x04_P2.50mm_Vertical
J5: Motor_2; JST_XH_B3B-XH-A_1x03_P2.50mm_Vertical
J6: Motor_1; JST_XH_B3B-XH-A_1x03_P2.50mm_Vertical
J7: I2C_2; JST_XH_B4B-XH-A_1x04_P2.50mm_Vertical
J8: Light Sensor; JST_XH_B3B-XH-A_1x03_P2.50mm_Vertical
J9: Green_Red_Led; JST_XH_B3B-XH-A_1x03_P2.50mm_Vertical
J10: Door_Open; JST_XH_B2B-XH-A_1x02_P2.50mm_Vertical
J11: Door_Closed; JST_XH_B2B-XH-A_1x02_P2.50mm_Vertical
J12: I2C_3; JST_XH_B4B-XH-A_1x04_P2.50mm_Vertical
R1: 2K2; R_Axial_DIN0207_L6.3mm_D2.5mm_P10.16mm_Horizontal
R2: 220; R_Axial_DIN0207_L6.3mm_D2.5mm_P10.16mm_Horizontal
SW1: PowerSwitch; PinHeader_1x02_P2.54mm_Vertical
U1, U3: INA226-Sense_I2C; INA226
U2: ESP32-DEVKIT-V1
U4: L7805CV; TO-220-3; MPN L7805CV; Digi-Key_PN 497-1443-5-ND

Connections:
+3V3: J4.4, J7.4, J8.1, J12.4, U1.8 (VCC), U2.16 (3V3), U3.8 (VCC)
D0: J8.3, U2.6 (GPIO32_ADC1-CH4_RTC-GPIO9)
Door_Closed: J11.2, U2.5 (GPIO35_ADC1-CH7_RTC-GPIO5)
Door_Open: J10.2, U2.4 (GPIO34_ADC1-CH6_RTC-GPIO4)
Enable_A: J6.1, U2.30 (GPIO23_VSPI-MOSI)
Enable_B: J5.1, U2.25 (GPIO19_VSPI-MISO)
GND: DC-DC1.I- (IN-), DC-DC1.O- (OUT-), J1.2, J2.2, J3.2, J4.3, J7.3, J8.2, J9.1, J10.1, J11.1, J12.3, U1.7 (GND), U2.14 (GND), U2.17 (GND), U3.7 (GND), U4.2 (GND)
Green: R2.2, U2.8 (GPIO25_ADC2-CH8_DAC1_RTC-GPIO6)
Input_1: J6.2, U2.12 (GPIO12_ADC2-CH5_HSPI-MISO_RTC-GPIO15)
Input_2: J6.3, U2.13 (GPIO13_ADC2-CH4_HSPI-MOSI_RTC-GPIO14)
Input_3: J5.3, U2.11 (GPIO14_ADC2-CH6_HSPI-CLK_RTC-GPIO16)
Input_4: J5.2, U2.24 (GPIO18_VSPI-CLK)
unnamed: DC-DC1.I+ (IN+), SW1.2, U1.3 (VBS), U1.9 (IN1+)
unnamed: DC-DC1.O+ (OUT+), U3.3 (VBS), U3.9 (IN1+), U4.1 (IN)
unnamed: J1.1, SW1.1
unnamed: J2.1, U1.10 (IN1-)
unnamed: J3.1, U3.10 (IN1-)
unnamed: J9.2, R1.1
unnamed: J9.3, R2.1
unnamed: U2.15 (VIN), U4.3 (OUT)
RED: R1.2, U2.9 (GPIO26_ADC2-CH9_DAC2_RTC-GPIO7)
SCL: J4.2, J7.2, J12.2, U1.5 (SCL), U2.29 (GPIO22_I2C-SCL), U3.5 (SCL)
SDA: J4.1, J7.1, J12.1, U1.6 (SDA), U2.26 (GPIO21_I2C-SDA), U3.6 (SDA)

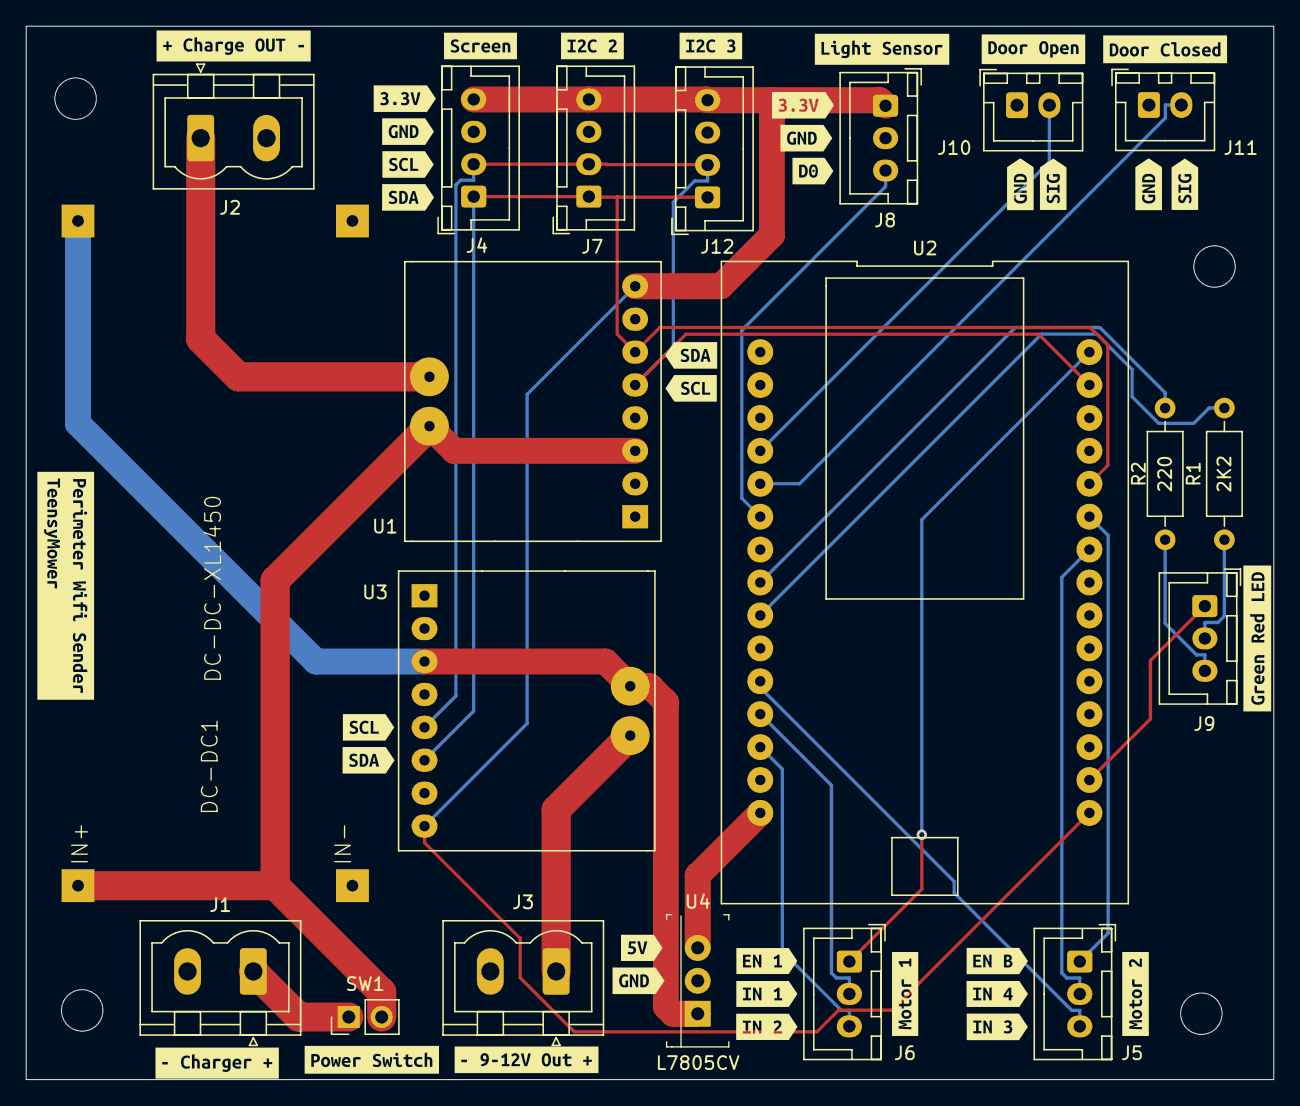
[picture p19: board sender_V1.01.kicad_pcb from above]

Board: 2 copper layers, 96.3 x 81.3 mm, 61 parts (0 on the bottom side), 23 nets.

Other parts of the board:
kibuzzard-63A206E8: G***; kibuzzard-63A206E8
kibuzzard-63A20733: G***; kibuzzard-63A20733
kibuzzard-6384DEE7: G***; kibuzzard-6384DEE7
kibuzzard-6384DF75: G***; kibuzzard-6384DF75
kibuzzard-6384DFD2: G***; kibuzzard-6384DFD2
kibuzzard-6384E1E3: G***; kibuzzard-6384E1E3
kibuzzard-6384E1F1: G***; kibuzzard-6384E1F1
kibuzzard-6384E6A4: G***; kibuzzard-6384E6A4
kibuzzard-6384E6B7: G***; kibuzzard-6384E6B7
kibuzzard-6384E6DA: G***; kibuzzard-6384E6DA
kibuzzard-6384E6E7: G***; kibuzzard-6384E6E7
kibuzzard-6384E6FA: G***; kibuzzard-6384E6FA
kibuzzard-6384E007: G***; kibuzzard-6384E007
kibuzzard-6384E7AB: G***; kibuzzard-6384E7AB
kibuzzard-6384E7D3: G***; kibuzzard-6384E7D3
kibuzzard-6384E7EC: G***; kibuzzard-6384E7EC
kibuzzard-6384E8E9: G***; kibuzzard-6384E8E9
kibuzzard-6384E22C: G***; kibuzzard-6384E22C
kibuzzard-6384E78E: G***; kibuzzard-6384E78E
kibuzzard-6384E79B: G***; kibuzzard-6384E79B
kibuzzard-6384E93F: G***; kibuzzard-6384E93F
kibuzzard-6384E95B: G***; kibuzzard-6384E95B
kibuzzard-6384E151: G***; kibuzzard-6384E151
kibuzzard-6384E173: G***; kibuzzard-6384E173
kibuzzard-6384E189: G***; kibuzzard-6384E189
kibuzzard-6384E214: G***; kibuzzard-6384E214
kibuzzard-6384E652: G***; kibuzzard-6384E652
kibuzzard-6384E711: G***; kibuzzard-6384E711
kibuzzard-6384E779: G***; kibuzzard-6384E779
kibuzzard-6384E802: G***; kibuzzard-6384E802
kibuzzard-6384E847: G***; kibuzzard-6384E847
kibuzzard-6384E870: G***; kibuzzard-6384E870
kibuzzard-6384E880: G***; kibuzzard-6384E880
kibuzzard-6384E924: G***; kibuzzard-6384E924
kibuzzard-6384E969: G***; kibuzzard-6384E969
kibuzzard-642943C6: G***; kibuzzard-642943C6
kibuzzard-63696024: G***; kibuzzard-63696024

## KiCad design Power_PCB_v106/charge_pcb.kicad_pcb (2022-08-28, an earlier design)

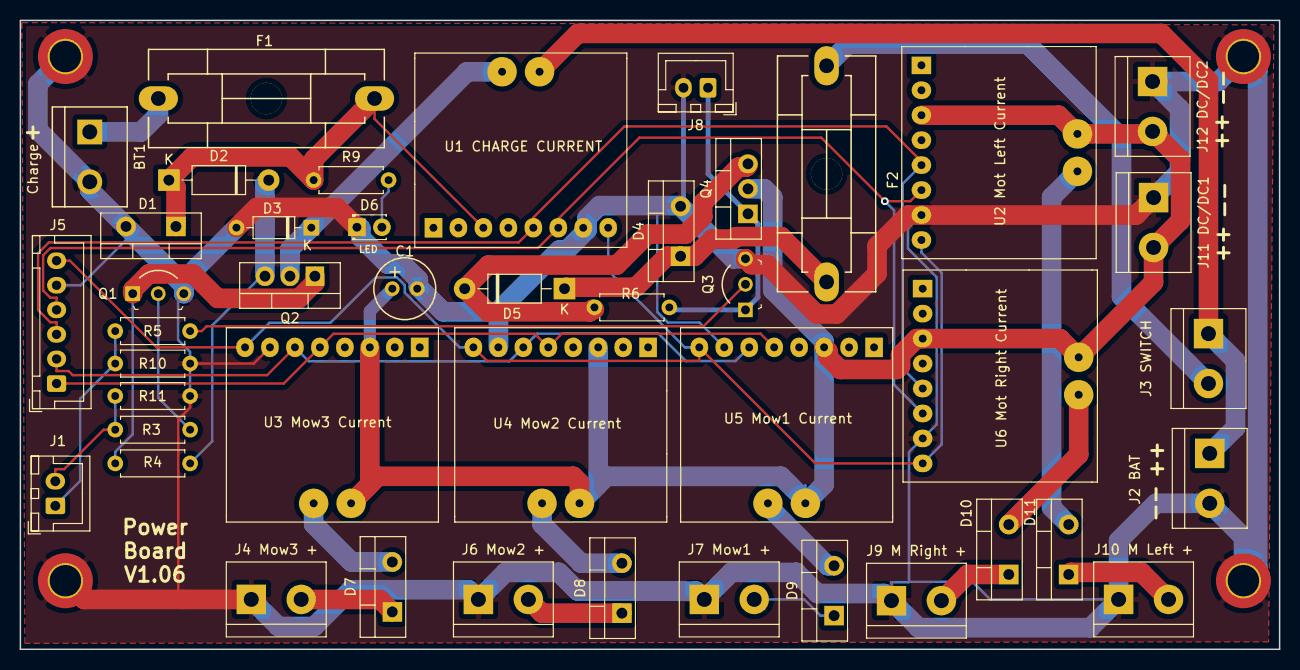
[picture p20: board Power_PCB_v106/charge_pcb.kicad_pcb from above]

Board: 2 copper layers, 128.1 x 64.0 mm, 48 parts (0 on the bottom side), 32 nets.

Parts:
BT1: Charge; Anschlussklemme_2P_RM5,08
C1: 100uF; Elko_vert_11.2x6.3mm_RM2.5
D1, D4, D7, D8, D9, D10, D11: MBR1045; TO-220-2_Vertical
D2, D5: SB1240; D_DO-41_SOD81_P10.16mm_Horizontal
D3: 1N4148; D_DO-35_SOD27_P7.62mm_Horizontal
D6: LED; LED_D1.8mm_W3.3mm_H2.4mm
F1: 5A; Fuseholder_Reichelt_PL112000
F2: 10A; Fuseholder_Reichelt_PL112000
H1, H2, H3, H4: MountingHole_Pad; MountingHole_3.2mm_M3_DIN965_Pad_TopBottom
J1: Main_PCB2; JST_XH_B2B-XH-A_1x02_P2.50mm_Vertical
J2 BAT: Battery; TerminalBlock_bornier-2_P5.08mm
J3 SWITCH: Power Switch; TerminalBlock_bornier-2_P5.08mm
J4 Mow3 +: Mow3; TerminalBlock_bornier-2_P5.08mm
J5: Main_PCB1; JST_XH_B6B-XH-A_1x06_P2.50mm_Vertical
J6 Mow2 +: Mow2; TerminalBlock_bornier-2_P5.08mm
J7 Mow1 +: Mow1; TerminalBlock_bornier-2_P5.08mm
J8: Start; JST_XH_B2B-XH-A_1x02_P2.50mm_Vertical
J9 M Right +: Mot_Right; TerminalBlock_bornier-2_P5.08mm
J10 M Left +: Mot_Left; TerminalBlock_bornier-2_P5.08mm
J11 DC/DC1: DC/DC1; TerminalBlock_bornier-2_P5.08mm
J12 DC/DC2: DC/DC2; TerminalBlock_bornier-2_P5.08mm
Q1, Q3: BC547C; TO-92-3_Formed_Leads
Q2, Q4: IRF9540N; TO-220-3_Vertical
R3, R4, R5, R6: 4k7; R_Axial_DIN0207_L6.3mm_D2.5mm_P7.62mm_Horizontal
R9: 4.7kO; R_Axial_DIN0207_L6.3mm_D2.5mm_P7.62mm_Horizontal
R10, R11: 2k2; R_Axial_DIN0207_L6.3mm_D2.5mm_P7.62mm_Horizontal
U1 CHARGE CURRENT, U2 Mot Left Current, U3 Mow3 Current, U4 Mow2 Current, U5 Mow1 Current, U6 Mot Right Current: INA226

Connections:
+3V3: J5.6, U1 CHARGE CURRENT.8, U2 Mot Left Current.8, U3 Mow3 Current.8, U4 Mow2 Current.8, U5 Mow1 Current.8, U6 Mot Right Current.8
GND: BT1.2, C1.2, D1.2, D3.2, D4.2, D6.1, H1.1, H2.1, H3.1, H4.1, J2 BAT.2, J4 Mow3 +.1, J5.5, J6 Mow2 +.1, J7 Mow1 +.1, J8.2, J9 M Right +.1, J10 M Left +.1, J11 DC/DC1.1, J12 DC/DC2.1, Q1.3, Q3.3, R10.2, R11.2, U1 CHARGE CURRENT.7, U2 Mot Left Current.7, U3 Mow3 Current.7, U4 Mow2 Current.7, U5 Mow1 Current.7, U6 Mot Right Current.7
unnamed: BT1.1, F1.1
unnamed: D2.2, Q2.3, R4.1
unnamed: D3.1, Q2.2, U1 CHARGE CURRENT.9
unnamed: D4.1, D5.1, F2.2
unnamed: D5.2, Q4.3, R6.1
unnamed: D6.2, R9.2
unnamed: D7.1, J4 Mow3 +.2
unnamed: D7.2, U3 Mow3 Current.10
unnamed: D8.1, J6 Mow2 +.2
unnamed: D8.2, U4 Mow2 Current.10
unnamed: D9.1, J7 Mow1 +.2
unnamed: D9.2, U5 Mow1 Current.10
unnamed: D10.1, J9 M Right +.2
unnamed: D10.2, U6 Mot Right Current.10
unnamed: D11.1, J10 M Left +.2
unnamed: D11.2, U2 Mot Left Current.10
unnamed: F2.1, J3 SWITCH.2
unnamed: J2 BAT.1, J3 SWITCH.1, U1 CHARGE CURRENT.10
unnamed: J8.1, Q3.1, Q4.1, R6.2
unnamed: Q1.1, Q2.1, R4.2
unnamed: Q1.2, R3.1
unnamed: Q3.2, R5.2
SCL0: J5.3, U1 CHARGE CURRENT.5, U2 Mot Left Current.5, U6 Mot Right Current.5
SCL1: J5.1, U3 Mow3 Current.5, U4 Mow2 Current.5, U5 Mow1 Current.5
SDA0: J5.4, U1 CHARGE CURRENT.6, U2 Mot Left Current.6, U6 Mot Right Current.6
SDA1: J5.2, U3 Mow3 Current.6, U4 Mow2 Current.6, U5 Mow1 Current.6
V_Bat: C1.1, J11 DC/DC1.2, J12 DC/DC2.2, Q4.2, U2 Mot Left Current.3, U2 Mot Left Current.9, U3 Mow3 Current.3, U3 Mow3 Current.9, U4 Mow2 Current.3, U4 Mow2 Current.9, U5 Mow1 Current.3, U5 Mow1 Current.9, U6 Mot Right Current.3, U6 Mot Right Current.9
V_Charge: D1.1, D2.1, F1.2, R9.1, U1 CHARGE CURRENT.3
pinBatterySwitch: J1.1, R5.1, R10.1
pinChargeEnable: J1.2, R3.2, R11.1

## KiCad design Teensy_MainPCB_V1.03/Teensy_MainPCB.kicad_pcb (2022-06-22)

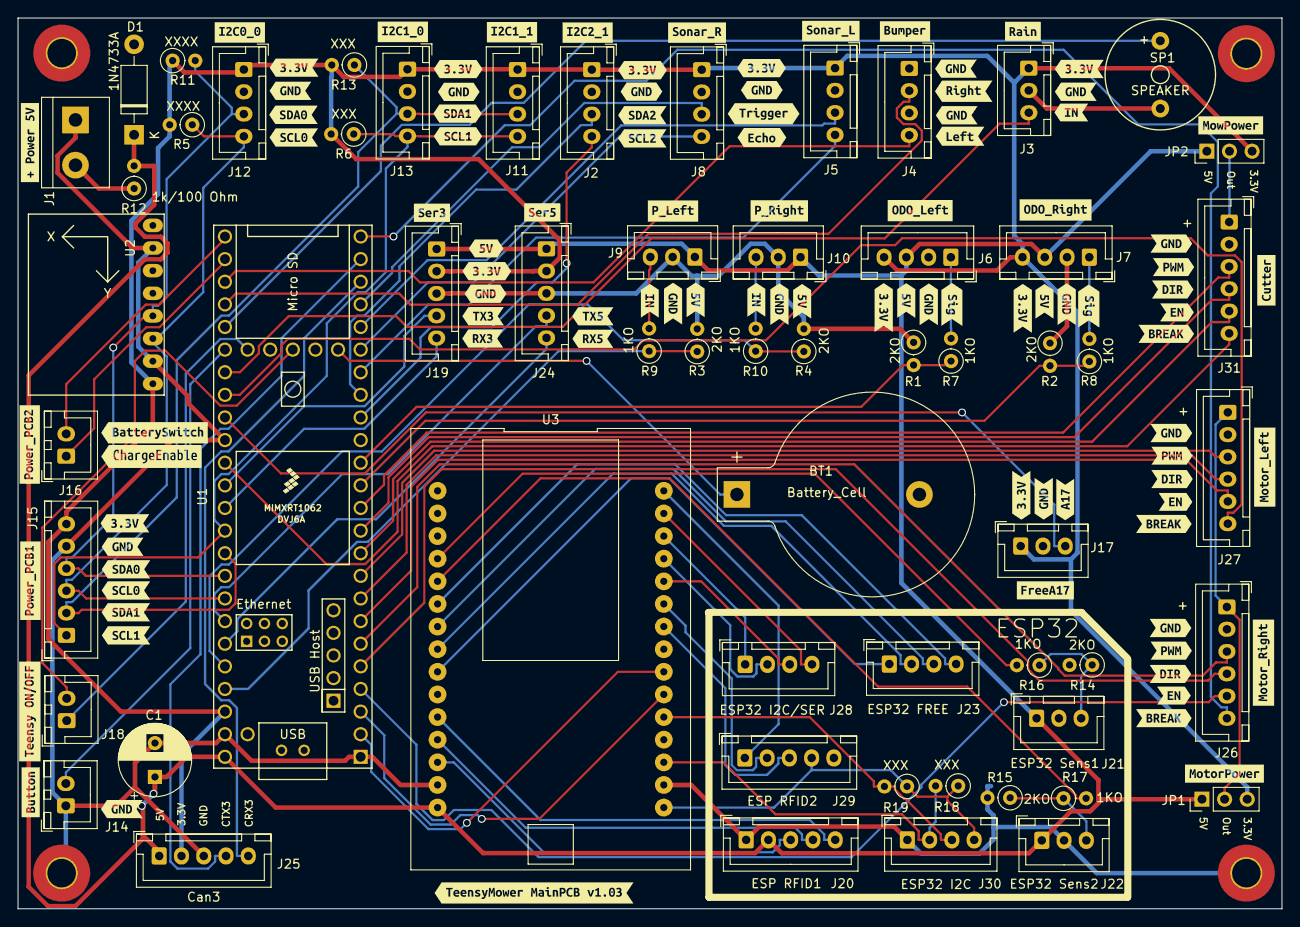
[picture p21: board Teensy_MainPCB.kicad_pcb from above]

Board: 2 copper layers, 141.9 x 100.0 mm, 160 parts (0 on the bottom side), 76 nets.

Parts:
BT1: Battery_Cell; BatteryHolder_Keystone_103_1x20mm
C1: CP1; CP_Radial_D8.0mm_P3.80mm
D1: 1N4733A; D_DO-41_SOD81_P10.16mm_Horizontal
H1, H2, H3, H4: MountingHole_Pad; MountingHole_3.2mm_M3_Pad_TopBottom
J1: 5V IN; TerminalBlock_bornier-2_P5.08mm
J2: I2C2_0; JST_XH_B4B-XH-A_1x04_P2.50mm_Vertical
J3: Rain; JST_XH_B3B-XH-A_1x03_P2.50mm_Vertical
J4: Bumper; JST_XH_B4B-XH-A_1x04_P2.50mm_Vertical
J5: Sonar_L; JST_XH_B4B-XH-A_1x04_P2.50mm_Vertical
J6: ODO_Left; JST_XH_B4B-XH-A_1x04_P2.50mm_Vertical
J7: ODO_Right; JST_XH_B4B-XH-A_1x04_P2.50mm_Vertical
J8: Sonar_R; JST_XH_B4B-XH-A_1x04_P2.50mm_Vertical
J9: P_Left; JST_XH_B3B-XH-A_1x03_P2.50mm_Vertical
J10: P_Right; JST_XH_B3B-XH-A_1x03_P2.50mm_Vertical
J11: I2C1_1; JST_XH_B4B-XH-A_1x04_P2.50mm_Vertical
J12: I2C0_0; JST_XH_B4B-XH-A_1x04_P2.50mm_Vertical
J13: I2C1_0; JST_XH_B4B-XH-A_1x04_P2.50mm_Vertical
J14: Button; JST_XH_B2B-XH-A_1x02_P2.50mm_Vertical
J15: Power_PCB1; JST_XH_B6B-XH-A_1x06_P2.50mm_Vertical
J16: Power_PCB2; JST_XH_B2B-XH-A_1x02_P2.50mm_Vertical
J17: FreeA17; JST_XH_B3B-XH-A_1x03_P2.50mm_Vertical
J18: Teensy On/Off; JST_XH_B2B-XH-A_1x02_P2.50mm_Vertical
J19: Ser3; JST_XH_B5B-XH-A_1x05_P2.50mm_Vertical
J20: ESP RFID1; JST_XH_B5B-XH-A_1x05_P2.50mm_Vertical
J21: ESP32 Sens1; JST_XH_B3B-XH-A_1x03_P2.50mm_Vertical
J22: ESP32 Sens2; JST_XH_B3B-XH-A_1x03_P2.50mm_Vertical
J23: ESP32 FREE; JST_XH_B4B-XH-A_1x04_P2.50mm_Vertical
J24: Ser5; JST_XH_B5B-XH-A_1x05_P2.50mm_Vertical
J25: Can3; JST_XH_B5B-XH-A_1x05_P2.50mm_Vertical
J26: Motor_Right; JST_XH_B6B-XH-A_1x06_P2.50mm_Vertical
J27: Motor_Left; JST_XH_B6B-XH-A_1x06_P2.50mm_Vertical
J28: ESP32 I2C/SER; JST_XH_B4B-XH-A_1x04_P2.50mm_Vertical
J29: ESP RFID2; JST_XH_B5B-XH-A_1x05_P2.50mm_Vertical
J30: ESP32 I2C; JST_XH_B4B-XH-A_1x04_P2.50mm_Vertical
J31: Cutter; JST_XH_B6B-XH-A_1x06_P2.50mm_Vertical
JP1: MotorPower; PinHeader_1x03_P2.54mm_Vertical
JP2: CutterPower; PinHeader_1x03_P2.54mm_Vertical
R1, R2, R3, R4, R14, R15: 2KO; R_Axial_DIN0207_L6.3mm_D2.5mm_P2.54mm_Vertical
R5, R11: XXXX; R_Axial_DIN0207_L6.3mm_D2.5mm_P2.54mm_Vertical
R6, R13, R18, R19: XXX; R_Axial_DIN0207_L6.3mm_D2.5mm_P2.54mm_Vertical
R7, R8, R9, R10, R16, R17: 1KO; R_Axial_DIN0207_L6.3mm_D2.5mm_P2.54mm_Vertical
R12: 1k/100 Ohm; R_Axial_DIN0207_L6.3mm_D2.5mm_P2.54mm_Vertical
SP1: SPEAKER; Buzzer_12x9.5RM7.6
U1: Teensy4.1; Teensy41
U2: GY-521
U3: ESP32-DEVKIT-V1
kibuzzard-62AA1DDF: G***; kibuzzard-62AA1DDF
kibuzzard-62AA1E85: G***; kibuzzard-62AA1E85
kibuzzard-62AA1F05: G***; kibuzzard-62AA1F05
kibuzzard-62AA3A43: G***; kibuzzard-62AA3A43
kibuzzard-62AA3A85: G***; kibuzzard-62AA3A85
kibuzzard-62AA3B12: G***; kibuzzard-62AA3B12
kibuzzard-62AA34D8: G***; kibuzzard-62AA34D8
kibuzzard-62AA39DC: G***; kibuzzard-62AA39DC
kibuzzard-62AA347B: G***; kibuzzard-62AA347B
kibuzzard-62AA353C: G***; kibuzzard-62AA353C
kibuzzard-62AA3447: G***; kibuzzard-62AA3447
kibuzzard-62AA3566: G***; kibuzzard-62AA3566
kibuzzard-62AB5E06: G***; kibuzzard-62AB5E06
kibuzzard-62AB5E66: G***; kibuzzard-62AB5E66
kibuzzard-62AB5ED1: G***; kibuzzard-62AB5ED1
kibuzzard-62AB5F2F: G***; kibuzzard-62AB5F2F
kibuzzard-62AB5F67: G***; kibuzzard-62AB5F67
kibuzzard-62AB5FC4: G***; kibuzzard-62AB5FC4
kibuzzard-62AB5FF2: G***; kibuzzard-62AB5FF2
kibuzzard-62AB6A77: G***; kibuzzard-62AB6A77
kibuzzard-62AB6A93: G***; kibuzzard-62AB6A93
kibuzzard-62AB6AFA: G***; kibuzzard-62AB6AFA
kibuzzard-62AB6B3D: G***; kibuzzard-62AB6B3D
kibuzzard-62AB6B9B: G***; kibuzzard-62AB6B9B
kibuzzard-62AB6BA8: G***; kibuzzard-62AB6BA8
kibuzzard-62AB6BF4: G***; kibuzzard-62AB6BF4
kibuzzard-62AB6CC8: G***; kibuzzard-62AB6CC8
kibuzzard-62AB6D7A: G***; kibuzzard-62AB6D7A
kibuzzard-62AB6EF0: G***; kibuzzard-62AB6EF0
kibuzzard-62AB6F91: G***; kibuzzard-62AB6F91
kibuzzard-62AB60B1: G***; kibuzzard-62AB60B1
kibuzzard-62AB62B6: G***; kibuzzard-62AB62B6
kibuzzard-62AB62D3: G***; kibuzzard-62AB62D3
kibuzzard-62AB63D2: G***; kibuzzard-62AB63D2
kibuzzard-62AB64C2: G***; kibuzzard-62AB64C2
kibuzzard-62AB64F2: G***; kibuzzard-62AB64F2
kibuzzard-62AB77E5: G***; kibuzzard-62AB77E5
kibuzzard-62AB634F: G***; kibuzzard-62AB634F
kibuzzard-62AB639B: G***; kibuzzard-62AB639B
kibuzzard-62AB756D: G***; kibuzzard-62AB756D
kibuzzard-62AB767F: G***; kibuzzard-62AB767F
kibuzzard-62AB774A: G***; kibuzzard-62AB774A
kibuzzard-62AB778D: G***; kibuzzard-62AB778D
kibuzzard-62AB789F: G***; kibuzzard-62AB789F
kibuzzard-62AB6021: G***; kibuzzard-62AB6021
kibuzzard-62AB6109: G***; kibuzzard-62AB6109
kibuzzard-62AB6374: G***; kibuzzard-62AB6374
kibuzzard-62AB6557: G***; kibuzzard-62AB6557
kibuzzard-62AB7031: G***; kibuzzard-62AB7031
kibuzzard-62AC4CEE: G***; kibuzzard-62AC4CEE
kibuzzard-62AC4D6D: G***; kibuzzard-62AC4D6D
kibuzzard-62AC8CBD: G***; kibuzzard-62AC8CBD
kibuzzard-62AC8CC8: G***; kibuzzard-62AC8CC8
kibuzzard-62AC8CD7: G***; kibuzzard-62AC8CD7
kibuzzard-62AC8CE7: G***; kibuzzard-62AC8CE7
kibuzzard-62AC8CFB: G***; kibuzzard-62AC8CFB
kibuzzard-62AC8D1B: G***; kibuzzard-62AC8D1B
kibuzzard-62AC8D10: G***; kibuzzard-62AC8D10
kibuzzard-62AC8D87: G***; kibuzzard-62AC8D87
kibuzzard-62AC8DAF: G***; kibuzzard-62AC8DAF
kibuzzard-62AC8DEE: G***; kibuzzard-62AC8DEE
kibuzzard-62AC8E7D: G***; kibuzzard-62AC8E7D
kibuzzard-62AC8E96: G***; kibuzzard-62AC8E96
kibuzzard-62AC8EE6: G***; kibuzzard-62AC8EE6
kibuzzard-62AC8F0E: G***; kibuzzard-62AC8F0E
kibuzzard-62AC8F57: G***; kibuzzard-62AC8F57
kibuzzard-62AC8F80: G***; kibuzzard-62AC8F80
kibuzzard-62AC8F92: G***; kibuzzard-62AC8F92
kibuzzard-62AC8FB5: G***; kibuzzard-62AC8FB5
kibuzzard-62AC8FDD: G***; kibuzzard-62AC8FDD
kibuzzard-62AC8FEE: G***; kibuzzard-62AC8FEE
kibuzzard-62AC52F4: G***; kibuzzard-62AC52F4
kibuzzard-62AC90B9: G***; kibuzzard-62AC90B9
kibuzzard-62AC90FB: G***; kibuzzard-62AC90FB
kibuzzard-62AC91A3: G***; kibuzzard-62AC91A3
kibuzzard-62AC91BB: G***; kibuzzard-62AC91BB
kibuzzard-62AC91C5: G***; kibuzzard-62AC91C5
kibuzzard-62AC91DF: G***; kibuzzard-62AC91DF
kibuzzard-62AC91F0: G***; kibuzzard-62AC91F0
kibuzzard-62AC92C8: G***; kibuzzard-62AC92C8
kibuzzard-62AC93D0: G***; kibuzzard-62AC93D0
kibuzzard-62AC95A7: G***; kibuzzard-62AC95A7
kibuzzard-62AC95BD: G***; kibuzzard-62AC95BD
kibuzzard-62AC95C9: G***; kibuzzard-62AC95C9
kibuzzard-62AC916E: G***; kibuzzard-62AC916E
kibuzzard-62AC917A: G***; kibuzzard-62AC917A
kibuzzard-62AC918B: G***; kibuzzard-62AC918B
kibuzzard-62AC932E: G***; kibuzzard-62AC932E
kibuzzard-62AC961B: G***; kibuzzard-62AC961B
kibuzzard-62AC9112: G***; kibuzzard-62AC9112
kibuzzard-62AC9161: G***; kibuzzard-62AC9161
kibuzzard-62AC9196: G***; kibuzzard-62AC9196
kibuzzard-62AC9203: G***; kibuzzard-62AC9203
kibuzzard-62AC9315: G***; kibuzzard-62AC9315
kibuzzard-62AC9376: G***; kibuzzard-62AC9376
kibuzzard-62AC9630: G***; kibuzzard-62AC9630
kibuzzard-62AC9639: G***; kibuzzard-62AC9639

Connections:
+3V3: J2.1, J3.1, J5.1, J6.4, J7.4, J8.1, J11.1, J12.1, J13.1, J15.6, J17.1, J19.2, J24.2, J25.2, JP1.3, JP2.3, R5.2, R6.2, R11.1, R13.2, U1.46 (3V3), U2.1 (VCC)
+5V: C1.1, D1.1 (K), J6.3, J7.3, J9.1, J10.1, J19.1, J20.2, J21.1, J22.1, J24.1, J25.1, JP1.1, JP2.1, R12.2, U1.48 (VIN), U3.15 (VIN)
CRX3: J25.5, U1.22 (30_CRX3)
CTX3: J25.4, U1.23 (31_CTX3)
FreeA17: J17.3, U1.33 (41_A17)
GND: BT1.2 (-), C1.2, D1.2 (A), H1.1, H2.1, H3.1, H4.1, J1.1, J2.2, J3.2, J4.1, J4.3, J5.2, J6.2, J7.2, J8.2, J9.2, J10.2, J11.2, J12.2, J13.2, J14.1, J15.5, J17.2, J19.3, J20.1, J21.2, J22.2, J24.3, J25.3, J26.2, J27.2, J30.1, J31.2, R1.1, R2.1, R3.2, R4.2, R14.2, R15.2, SP1.1, U1.1 (GND), U1.34 (GND), U1.47 (GND), U2.2 (GND), U2.7 (AD0), U3.14 (GND), U3.17 (GND)
unnamed: BT1.1 (+), U1.50 (VBAT)
unnamed: J1.2, R12.1
unnamed: J6.1, R7.2
unnamed: J7.1, R8.2
unnamed: J9.3, R9.2
unnamed: J10.3, R10.2
unnamed: J18.1, U1.54 (ON_OFF)
unnamed: J18.2, U1.52 (GND)
unnamed: J20.3, U3.13 (GPIO13_ADC2-CH4_HSPI-MOSI_RTC-GPIO14)
unnamed: J20.4, U3.12 (GPIO12_ADC2-CH5_HSPI-MISO_RTC-GPIO15)
unnamed: J20.5, U3.11 (GPIO14_ADC2-CH6_HSPI-CLK_RTC-GPIO16)
unnamed: J21.3, R14.1, R16.1
unnamed: J22.3, R15.1, R17.1
unnamed: J23.1, U3.9 (GPIO26_ADC2-CH9_DAC2_RTC-GPIO7)
unnamed: J23.2, U3.8 (GPIO25_ADC2-CH8_DAC1_RTC-GPIO6)
unnamed: J23.3, U3.7 (GPIO33_ADC1-CH5_RTC-GPIO8)
unnamed: J23.4, U3.6 (GPIO32_ADC1-CH4_RTC-GPIO9)
unnamed: J26.1, J27.1, JP1.2
unnamed: J28.1, U3.28 (GPIO1_UART0-TX)
unnamed: J28.2, U3.27 (GPIO3__UART0-RX)
unnamed: J28.3, U3.26 (GPIO21_I2C-SDA)
unnamed: J28.4, U3.29 (GPIO22_I2C-SCL)
unnamed: J29.1, U3.30 (GPIO23_VSPI-MOSI)
unnamed: J29.2, U3.25 (GPIO19_VSPI-MISO)
unnamed: J29.3, U3.24 (GPIO18_VSPI-CLK)
unnamed: J29.4, J30.4, R18.1, R19.1, U3.16 (3V3)
unnamed: J30.2, R18.2, U3.18 (GPIO15_ADC2-CH3_HSPI-CS0_RTC-GPIO13)
unnamed: J30.3, R19.2, U3.20 (GPIO4_ADC2-CH0_RTC-GPIO10)
unnamed: J31.1, JP2.2
unnamed: R16.2, U3.4 (GPIO34_ADC1-CH6_RTC-GPIO4)
unnamed: R17.2, U3.5 (GPIO35_ADC1-CH7_RTC-GPIO5)
RX1: U1.2 (0_RX1_CRX2_CS1), U3.22 (TX2)
RX3: J19.5, U1.37 (15_A1_RX3_SPDIF_IN)
RX5: J24.5, U1.43 (21_A7_RX5_BCLK1)
SCL0: J12.4, J15.3, R5.1, U1.41 (19_A5_SCL), U2.3 (SCL)
SCL1: J11.4, J13.4, J15.1, R6.1, U1.38 (16_A2_RX4_SCL1)
SCL2: J2.4, U1.16 (24_A10_TX6_SCL2)
SDA0: J12.3, J15.4, R11.2, U1.40 (18_A4_SDA), U2.4 (SDA)
SDA1: J11.3, J13.3, J15.2, R13.1, U1.39 (17_A3_TX4_SDA1)
SDA2: J2.3, U1.17 (25_A11_RX6_SDA2)
TX1: U1.3 (1_TX1_CTX2_MISO1), U3.21 (RX2)
TX3: J19.4, U1.36 (14_A0_TX3_SPDIF_OUT)
TX5: J24.4, U1.42 (20_A6_TX5_LRCLK1)
pinBatterySwitch: J16.2, U1.25 (33_MCLK2)
pinBumperLeft: J4.4, U1.27 (35_TX8)
pinBumperRight: J4.2, U1.28 (36_CS)
pinButton: J14.2, U1.30 (38_CS1_IN1)
pinBuzzer: SP1.2, U1.29 (37_CS)
pinChargeEnable: J16.1, U1.26 (34_RX8)
pinMotorLeftBreak: J27.6, U1.32 (40_A16)
pinMotorLeftDir: J27.4, U1.8 (6_OUT1D)
pinMotorLeftEnable: J27.5, U1.7 (5_IN2)
pinMotorLeftPWM: J27.3, U1.9 (7_RX2_OUT1A)
pinMotorMowBreak: J31.6, U1.35 (13_SCK_LED)
pinMotorMowDir: J31.4, U1.11 (9_OUT1C)
pinMotorMowEnable: J31.5, U1.10 (8_TX2_IN1)
pinMotorMowPWM: J31.3, U1.12 (10_CS_MQSR)
pinMotorRightBreak: J26.6, U1.24 (32_OUT1B)
pinMotorRightDir: J26.4, U1.5 (3_LRCLK2)
pinMotorRightEnable: J26.5, U1.4 (2_OUT2)
pinMotorRightPWM: J26.3, U1.6 (4_BCLK2)
pinOdometryLeft: R1.2, R7.1, U1.14 (12_MISO_MQSL)
pinOdometryRight: R2.2, R8.1, U1.13 (11_MOSI_CTX1)
pinPerimeterLeft: R3.1, R9.1, U1.45 (23_A9_CRX1_MCLK1)
pinPerimeterRight: R4.1, R10.1, U1.44 (22_A8_CTX1)
pinRain: J3.3, U1.31 (39_MISO1_OUT1A)
pinSonarLeftEcho: J5.4, U1.18 (26_A12_MOSI1)
pinSonarLeftTrigger: J5.3, U1.20 (28_RX7)
pinSonarRightEcho: J8.4, U1.19 (27_A13_SCK1)
pinSonarRightTrigger: J8.3, U1.21 (29_TX7)

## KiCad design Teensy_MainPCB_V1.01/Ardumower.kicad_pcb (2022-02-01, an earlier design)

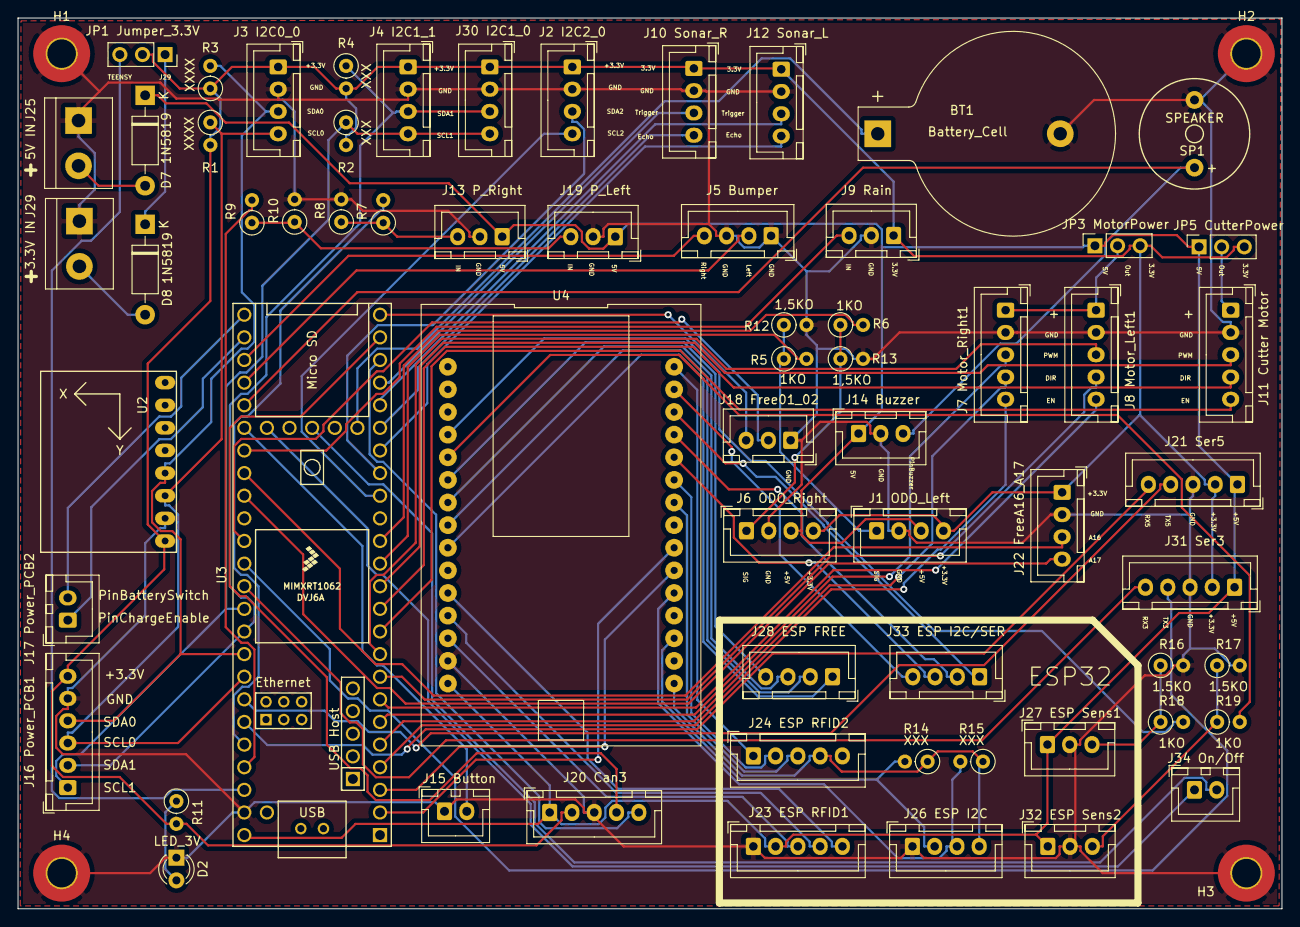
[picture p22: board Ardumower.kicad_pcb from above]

Board: 2 copper layers, 141.9 x 100.0 mm, 68 parts (0 on the bottom side), 80 nets.

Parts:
BT1: Battery_Cell; BatteryHolder_Keystone_103_1x20mm
D2: LED_3V; LED_D3.0mm
D7, D8: 1N5819; D_DO-41_SOD81_P10.16mm_Horizontal
H1, H2, H3, H4: MountingHole_Pad; MountingHole_3.2mm_M3_Pad_TopBottom
J1 ODO_Left: ODO_Left; JST_XH_B4B-XH-A_1x04_P2.50mm_Vertical
J2 I2C2_0: I2C2_0; JST_XH_B4B-XH-A_1x04_P2.50mm_Vertical
J3 I2C0_0: I2C0_0; JST_XH_B4B-XH-A_1x04_P2.50mm_Vertical
J4 I2C1_1: I2C1_1; JST_XH_B4B-XH-A_1x04_P2.50mm_Vertical
J5 Bumper: Bumper; JST_XH_B4B-XH-A_1x04_P2.50mm_Vertical
J6 ODO_Right: ODO_Right; JST_XH_B4B-XH-A_1x04_P2.50mm_Vertical
J7 Motor_Right1: Motor_Right1; JST_XH_B5B-XH-A_1x05_P2.50mm_Vertical
J8 Motor_Left1: Motor_Left1; JST_XH_B5B-XH-A_1x05_P2.50mm_Vertical
J9 Rain: Rain; JST_XH_B3B-XH-A_1x03_P2.50mm_Vertical
J10 Sonar_R: Sonar_R; JST_XH_B4B-XH-A_1x04_P2.50mm_Vertical
J11 Cutter Motor: Cutter; JST_XH_B5B-XH-A_1x05_P2.50mm_Vertical
J12 Sonar_L: Sonar_L; JST_XH_B4B-XH-A_1x04_P2.50mm_Vertical
J13 P_Right: P_Right; JST_XH_B3B-XH-A_1x03_P2.50mm_Vertical
J14 Buzzer: Buzzer; JST_XH_B3B-XH-A_1x03_P2.50mm_Vertical
J15 Button: Button; JST_XH_B2B-XH-A_1x02_P2.50mm_Vertical
J16 Power_PCB1: Power_PCB1; JST_XH_B6B-XH-A_1x06_P2.50mm_Vertical
J17 Power_PCB2: Power_PCB2; JST_XH_B2B-XH-A_1x02_P2.50mm_Vertical
J18 Free01_02: Free01_02; JST_XH_B3B-XH-A_1x03_P2.50mm_Vertical
J19 P_Left: P_Left; JST_XH_B3B-XH-A_1x03_P2.50mm_Vertical
J20 Can3: Can3; JST_XH_B5B-XH-A_1x05_P2.50mm_Vertical
J21 Ser5: Ser5; JST_XH_B5B-XH-A_1x05_P2.50mm_Vertical
J22 FreeA16_A17: FreeA16_A17; JST_XH_B4B-XH-A_1x04_P2.50mm_Vertical
J23 ESP RFID1: ESP RFID1; JST_XH_B5B-XH-A_1x05_P2.50mm_Vertical
J24 ESP RFID2: ESP RFID2; JST_XH_B5B-XH-A_1x05_P2.50mm_Vertical
J25: 5V IN; TerminalBlock_bornier-2_P5.08mm
J26 ESP I2C: ESP32 I2C; JST_XH_B4B-XH-A_1x04_P2.50mm_Vertical
J27 ESP Sens1: ESP32 Sens1; JST_XH_B3B-XH-A_1x03_P2.50mm_Vertical
J28 ESP FREE: ESP32 FREE; JST_XH_B4B-XH-A_1x04_P2.50mm_Vertical
J29: 3.3V IN; TerminalBlock_bornier-2_P5.08mm
J30 I2C1_0: I2C1_0; JST_XH_B4B-XH-A_1x04_P2.50mm_Vertical
J31 Ser3: Ser3; JST_XH_B5B-XH-A_1x05_P2.50mm_Vertical
J32 ESP Sens2: ESP32 Sens2; JST_XH_B3B-XH-A_1x03_P2.50mm_Vertical
J33 ESP I2C/SER: ESP32 I2C/SER; JST_XH_B4B-XH-A_1x04_P2.50mm_Vertical
J34 On/Off: Teensy On/Off; JST_XH_B2B-XH-A_1x02_P2.50mm_Vertical
JP1 Jumper_3.3V: Jumper_3.3V; PinSocket_1x03_P2.54mm_Vertical
JP3 MotorPower: MotorPower; PinSocket_1x03_P2.54mm_Vertical
JP5 CutterPower: CutterPower; PinSocket_1x03_P2.54mm_Vertical
R1, R3: XXXX; R_Axial_DIN0207_L6.3mm_D2.5mm_P2.54mm_Vertical
R2, R4, R14, R15: XXX; R_Axial_DIN0207_L6.3mm_D2.5mm_P2.54mm_Vertical
R5, R6, R7, R9, R18, R19: 1KO; R_Axial_DIN0207_L6.3mm_D2.5mm_P2.54mm_Vertical
R8, R10, R16, R17: 1.5KO; R_Axial_DIN0207_L6.3mm_D2.5mm_P2.54mm_Vertical
R11: 100; R_Axial_DIN0207_L6.3mm_D2.5mm_P2.54mm_Vertical
R12, R13: 1,5KO; R_Axial_DIN0207_L6.3mm_D2.5mm_P2.54mm_Vertical
SP1: SPEAKER; Buzzer_12x9.5RM7.6
U2: GY-521
U3: Teensy4.1; Teensy41
U4: ESP32-DEVKIT-V1

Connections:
+3V3: J1 ODO_Left.4, J2 I2C2_0.1, J3 I2C0_0.1, J4 I2C1_1.1, J6 ODO_Right.4, J9 Rain.1, J10 Sonar_R.1, J12 Sonar_L.1, J16 Power_PCB1.6, J20 Can3.2, J21 Ser5.2, J22 FreeA16_A17.1, J30 I2C1_0.1, J31 Ser3.2, JP1 Jumper_3.3V.2, JP3 MotorPower.3, JP5 CutterPower.3, R1.2, R2.2, R3.1, R4.2, R11.2, U2.1
+5V: D7.1, J1 ODO_Left.3, J6 ODO_Right.3, J13 P_Right.1, J14 Buzzer.1, J19 P_Left.1, J20 Can3.1, J21 Ser5.1, J23 ESP RFID1.2, J27 ESP Sens1.1, J31 Ser3.1, J32 ESP Sens2.1, JP3 MotorPower.1, JP5 CutterPower.1, U3.48, U4.15
CRX3: J20 Can3.5, U3.22
CTX3: J20 Can3.4, U3.23
Free01: J18 Free01_02.2, U3.35
Free02: J18 Free01_02.3, U3.24
FreeA16: J22 FreeA16_A17.3, U3.32
FreeA17: J22 FreeA16_A17.4, U3.33
GND: BT1.2, D2.1, H1.1, H2.1, H3.1, H4.1, J1 ODO_Left.2, J2 I2C2_0.2, J3 I2C0_0.2, J4 I2C1_1.2, J5 Bumper.1, J5 Bumper.3, J6 ODO_Right.2, J7 Motor_Right1.2, J8 Motor_Left1.2, J9 Rain.2, J10 Sonar_R.2, J11 Cutter Motor.2, J12 Sonar_L.2, J13 P_Right.2, J14 Buzzer.2, J15 Button.1, J16 Power_PCB1.5, J18 Free01_02.1, J19 P_Left.2, J20 Can3.3, J21 Ser5.3, J22 FreeA16_A17.2, J23 ESP RFID1.1, J25.1, J26 ESP I2C.1, J27 ESP Sens1.2, J29.1, J30 I2C1_0.2, J31 Ser3.3, J32 ESP Sens2.2, R8.2, R10.2, R12.2, R13.2, R16.2, R17.2, SP1.1, U2.2, U3.47, U4.14
unnamed: BT1.1, U3.50
unnamed: D2.2, R11.1
unnamed: D7.2, J25.2
unnamed: D8.1, JP1 Jumper_3.3V.1
unnamed: D8.2, J29.2
unnamed: J1 ODO_Left.1, R5.1, R12.1
unnamed: J6 ODO_Right.1, R6.1, R13.1
unnamed: J7 Motor_Right1.1, J8 Motor_Left1.1, JP3 MotorPower.2
unnamed: J11 Cutter Motor.1, JP5 CutterPower.2
unnamed: J13 P_Right.3, R7.1, R8.1
unnamed: J19 P_Left.3, R9.1, R10.1
unnamed: J23 ESP RFID1.3, U4.13
unnamed: J23 ESP RFID1.4, U4.12
unnamed: J23 ESP RFID1.5, U4.11
unnamed: J24 ESP RFID2.1, U4.30
unnamed: J24 ESP RFID2.2, U4.25
unnamed: J24 ESP RFID2.3, U4.24
unnamed: J24 ESP RFID2.4, J26 ESP I2C.4, R14.1, R15.1, U4.16
unnamed: J26 ESP I2C.2, R14.2, U4.18
unnamed: J26 ESP I2C.3, R15.2, U4.20
unnamed: J27 ESP Sens1.3, R16.1, R18.1
unnamed: J28 ESP FREE.1, U4.9
unnamed: J28 ESP FREE.2, U4.8
unnamed: J28 ESP FREE.3, U4.7
unnamed: J28 ESP FREE.4, U4.6
unnamed: J32 ESP Sens2.3, R17.1, R19.1
unnamed: J33 ESP I2C/SER.1, U4.28
unnamed: J33 ESP I2C/SER.2, U4.27
unnamed: J33 ESP I2C/SER.3, U4.26
unnamed: J33 ESP I2C/SER.4, U4.29
unnamed: J34 On/Off.1, U3.54
unnamed: J34 On/Off.2, U3.52
unnamed: JP1 Jumper_3.3V.3, U3.46
unnamed: R18.2, U4.4
unnamed: R19.2, U4.5
RX1: U3.2, U4.22
RX3: J31 Ser3.5, U3.37
RX5: J21 Ser5.5, U3.43
SCL0: J3 I2C0_0.4, J16 Power_PCB1.3, R1.1, U2.3, U3.41
SCL1: J4 I2C1_1.4, J16 Power_PCB1.1, J30 I2C1_0.4, R2.1, U3.38
SCL2: J2 I2C2_0.4, U3.16
SDA0: J3 I2C0_0.3, J16 Power_PCB1.4, R3.2, U2.4, U3.40
SDA1: J4 I2C1_1.3, J16 Power_PCB1.2, J30 I2C1_0.3, R4.1, U3.39
SDA2: J2 I2C2_0.3, U3.17
TX1: U3.3, U4.21
TX3: J31 Ser3.4, U3.36
TX5: J21 Ser5.4, U3.42
pinBatterySwitch: J17 Power_PCB2.2, U3.25
pinBumperLeft: J5 Bumper.4, U3.27
pinBumperRight: J5 Bumper.2, U3.28
pinButton: J15 Button.2, U3.30
pinBuzzer: J14 Buzzer.3, SP1.2, U3.29
pinChargeEnable: J17 Power_PCB2.1, U3.26
pinMotorLeftDir: J8 Motor_Left1.4, U3.8
pinMotorLeftEnable: J8 Motor_Left1.5, U3.7
pinMotorLeftPWM: J8 Motor_Left1.3, U3.9
pinMotorMowDir: J11 Cutter Motor.4, U3.11
pinMotorMowEnable: J11 Cutter Motor.5, U3.10
pinMotorMowPWM: J11 Cutter Motor.3, U3.12
pinMotorRightDir: J7 Motor_Right1.4, U3.5
pinMotorRightEnable: J7 Motor_Right1.5, U3.4
pinMotorRightPWM: J7 Motor_Right1.3, U3.6
pinOdometryLeft: R6.2, U3.14
pinOdometryRight: R5.2, U3.13
pinPerimeterLeft: R9.2, U3.45
pinPerimeterRight: R7.2, U3.44
pinRain: J9 Rain.3, U3.31
pinSonarLeftEcho: J12 Sonar_L.4, U3.18
pinSonarLeftTrigger: J12 Sonar_L.3, U3.20
pinSonarRightEcho: J10 Sonar_R.4, U3.19
pinSonarRightTrigger: J10 Sonar_R.3, U3.21

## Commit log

2021-11-04 Start Commit
    Clean start
    [TeensyPCB.kicad_pcb, TeensyPCB.kicad_sch, Teensy_4.0_Assembly.STEP]
2021-11-04 Rename Files
    Rename Files
    [TeensyPCB.kicad_pcb, TeensyPCB.kicad_sch, Teensy_4.0_Assembly.STEP]
2021-11-29 Small Changes in Layout Text
    [TeensyPCB-B_Cu_.gbl, TeensyPCB-B_Mask.gbs, TeensyPCB-B_Paste.gbp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]
2021-12-04 Add Shopping List
    [Shoppinglist.xls]
2022-02-01 Start Test
    [Ardumower-B_Cu.gbl, Ardumower-B_Cu.gbr, Ardumower-B_Mask.gbr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]
2022-02-01 Add Bigger Font
    New Version, with bigger Font. At present still without conductors
    [Teensy_MainPCB.kicad_pcb]
2022-02-01 Create _autosave-Teensy_MainPCB.kicad_pcb
    Bigger Font, small sorting changes
2022-02-01 Add Schematic PDF
    [Teensy_MainPCB.kicad_pcb, Teensy_MainPCB.sch]
2022-02-01 Front Correction
    [Teensy_MainPCB.kicad_pcb]
2022-02-02 First Route
    [Teensy_MainPCB.dsn, Teensy_MainPCB.kicad_pcb, Teensy_MainPCB_1.dsn]
2022-02-02 Rename Schematic
    [Teensy_MainPCB.sch]
2022-02-02 Add GND Plane
    [Teensy_MainPCB.kicad_pcb]
2022-02-04 Add ESP32 Files
    [Teensy_MainPCB.sch, sender_V1.00.kicad_pcb, sender_V1.00.sch]
2022-03-04 Small Changes in Labelling
    [Teensy_MainPCB.kicad_pcb, Teensy_MainPCB.sch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]
2022-03-05 Removed unused
    Remove unused Items and sorting new
    [Teensy_MainPCB-B_Cu.gbl, Teensy_MainPCB-B_Mask.gbs, Teensy_MainPCB-B_Paste.gbp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]
2022-05-13 Add MainPCB v1.03
    [Teensy_MainPCB-B_Cu.gbl, Teensy_MainPCB-B_Mask.gbs, Teensy_MainPCB-B_Paste.gbp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]
2022-05-13 Move Gerber Files
    [Ardumower-B_Cu.gbl, Ardumower-B_Mask.gbs, Ardumower-B_Paste.gbp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]
2022-05-13 Add Revision
    [Teensy_MainPCB.kicad_sch]
2022-05-15 Small changes
    [Teensy_MainPCB.kicad_pcb]
2022-06-22 Rework of chargePCB
    [Teensy_MainPCB.csv, Teensy_MainPCB.kicad_pcb, charge_pcb.kicad_pcb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]
2022-06-26 Rebuild Charge Board
    [charge_pcb.dsn, charge_pcb.kicad_pcb, charge_pcb.kicad_sch]
2022-06-26 Update Schematic PDF
2022-08-28 Don' know anymore
    [charge_pcb.kicad_pcb, charge_pcb.kicad_sch]
2022-09-03 Add Labeling and PCB Routing
    [charge_pcb.kicad_pcb, charge_pcb.kicad_sch, charge_pcb_1.dsn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]
2022-09-03 Removed old Pics
    [sender_V1.00.kicad_pcb, sender_V1.00.kicad_sch]
2022-09-03 Start Sender Design
    [sender_V1.00.kicad_sch]
2022-09-03 Start Design of Sender
    [Teensy_4.0_Assembly.STEP, sender_V1.00.kicad_pcb, sender_V1.00.kicad_sch]
2022-09-15 Add Gerber Files
    [charge_pcb-B_Cu.gbl, charge_pcb-B_Mask.gbs, charge_pcb-B_Paste.gbp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]
2022-12-20 Add Tracks
    Tracks added
    [sender_V1.00.dsn, sender_V1.00.kicad_pcb, sender_V1.00.kicad_sch]
2023-03-02 Add BOM File
    [sender_V1.00.kicad_pcb]
2023-04-02 Wifi Sender Update Label
    [Teensy_4.0_Assembly.STEP, charge_pcb.kicad_sch, charge_pcb.sch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]
2023-04-12 Start PowerPCB_v1.08
    [charge_pcb.dsn, charge_pcb.kicad_pcb, charge_pcb.kicad_sch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]
2023-04-24 Routing and change some Places
    [charge_pcb.kicad_pcb, charge_pcb_2.dsn, charge_pcb_3.dsn]
2023-04-28 Change Diode
    [charge_pcb.kicad_pcb, charge_pcb.kicad_sch]
2023-05-02 Routing and Gerber Files
    [charge_pcb-B_Cu.gbl, charge_pcb-B_Mask.gbs, charge_pcb-B_Paste.gbp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]
2023-05-02 Add Boom File
    [Parts_charge_pcb.csv, charge_pcb.csv]
2023-05-14 Connection from jumper changed
    [charge_pcb-B_Cu.gbl, charge_pcb-B_Mask.gbs, charge_pcb-B_Paste.gbp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]
2023-05-16 Add MBR1045
    [charge_pcb-B_Cu.gbl, charge_pcb-B_Mask.gbs, charge_pcb-B_Paste.gbp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]
2023-09-01 No Changes
    [charge_pcb.csv]
2023-12-05 Update PDF, Picture, Route
    Update the PDF File of the Board.
    Update PCB Picture.
    Route the PCB
    [charge_pcb.kicad_pcb, charge_pcb.kicad_sch, charge_pcb_2.dsn]
2023-12-05 Remove v1.08 PCB is Scrap
    [Parts_charge_pcb.csv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]
2023-12-05 Add some Logos to PCB
    [charge_pcb.kicad_pcb, charge_pcb.kicad_sch]
2024-02-07 Wrong Direktion of Q2 and Q4
    The Drain and Source Pin was in the wrong direction.
    [charge_pcb-B_Cu.gbl, charge_pcb-B_Mask.gbs, charge_pcb-B_Paste.gbp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]
2024-02-08 Small Updates
    [charge_pcb-B_Cu.gbl, charge_pcb-B_Mask.gbs, charge_pcb-B_Paste.gbp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]
2024-02-08 Change SDA SCL Footprint
    Ad new Schematic PDF and BOOM File
    [charge_pcb-B_Cu.gbl, charge_pcb-B_Mask.gbs, charge_pcb-B_Paste.gbp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]
2024-02-08 Add First SMALL PowerPCB
    [charge_pcb.kicad_pcb, charge_pcb.kicad_sch, charge_pcb_1.dsn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]
